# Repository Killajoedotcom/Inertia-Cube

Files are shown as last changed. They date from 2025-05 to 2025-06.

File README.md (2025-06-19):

## Welcome to the Inertia Cube Project!

INERTIA FOR GIT

The Inertia Cube (or i³) is a high speed FDM 3D printer that looks to optimize simplicity and provide a great entry point for all makers into the world of All Wheel Drive 3D printing. Its 300mm^3 build volume is built on a 3030 extrusion frame, optimized for ease of assembly, speed, and precision, while ensuring long-lasting performance and unmatched serviceability for enthusiasts who demand speed without compromising quality and those who need high printing uptime.

**World's first full kit printer featuring native Monolith Style Belt routing!** 

Thanks to the great work done over the last 2 years by CloakedWayne we have a fully optimized belt path for AWD printers that looks to minimize hardware and belt length, while providing incredible results in the process. We strongly encourage you to support his work via his [Kofi](https://ko-fi.com/cloakedwayne).

What makes it special? Some affectionately refer to the Inertia Cube as “baby’s first AWD printer” due to the simple assembly and design intent that makes it very easy to achieve near peak performance out of the printer regardless of DIY build experience.

Printer features:
- An external frame built from 3030 extrusions for extra rigidity
- Fixed gantry for maximum rigidity
- Easy Access electronics bay
- New extruder design which is a marriage of JaredC's G2SA and LDO's Orbiter2 parts to maximize extrusion force
- New single part toolhead design heavily inspired by Chirpy's Yavoth toolhead, optimized for rigidity and expanded compatibility
- Monolith AWD style gantry heavily inspired by CloakedWayne
- Linear rods for Y axis motion for easy install and simplicity
- 4 Z leadscrew motors for Quad Bed Leveling
- Support for USB or CAN Bus eddy current scanners as the Z probe (Beacon or Cartographer)
- Support for USB or CAN Bus Toolhead PCBs (LDO NH36, Fysetc H36, or BTT EBB36)
- Support for various hotends (starting with Rapido UHF, Dragon Ace Volcanao UHF, and Goliath)
- A latching sealed extrusion style front door

### FAQs:

**How do I stay up to date with this project?**

>Please Join our Discord here:
>
>Alt text for broken image link (https://discord.gg/da3cYmMA28)

**What is AWD (All Wheel Drive)?**
>While most CoreXY printers rely on a two-motor gantry drive system, the Inertia Cube leverages an advanced four-motor setup—two at the front and two at the back. This innovative design shortens the belt path, minimizes belt stretch, improves acceleration, and yields better input shaping results. With the added torque from the extra motors, acceleration performance is typically 1.5 times greater than traditional two-motor systems.

**What is the best performance hardware?**
>For optimal results, we recommend using LDO-42STH48-2504AH 1.8-degree motors paired with 20-tooth pulleys and EPDM GT2 belts if possible.

### Attributions
**Monolith Gantry** - [CloakedWayne](https://github.com/CloakedWayne/Monolith_Gantry_V2-VT)<br>
**Yavoth Toolhead** - [Chirpy](https://github.com/chirpy2605/voron/tree/main/V0/Yavoth)<br>
**G2** - [JaredC01](https://github.com/JaredC01/Galileo2)<br>
**Orbiter Project** - [Robert Lorincz](https://www.orbiterprojects.com/)<br>
**Clicky Clack** - [Whopping Pochard](https://github.com/tanaes/whopping_Voron_mods/tree/main/clickyclacky_door)<br>
**Inverted Electronics** - [LoganFraser](https://github.com/VoronDesign/VoronUsers/tree/main/printer_mods/LoganFraser/TridentInvertedElectronics)<br>

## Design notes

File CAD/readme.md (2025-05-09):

NOTE:<br>
<br>
Beta Frame Build is for those few people that have the 420mm horizontal and 555mm vertical 3030 extrusions. Some printed parts are resized to fit this build. Some fasteners and other non-printed parts still need to be added to this CAD model.<br>
<br>
Production Frame Build has been extended in XYZ to allow for a full 300mm cubic build volume, and will have 430mm horizontal and 600mm vertical 3030 extrusions. Contains all fasteners and other non-printed parts (although we are only human, and may have missed something).<br>

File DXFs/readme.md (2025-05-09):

NOTE:<br>
<br>
DXFs in the Beta folder are for those few people who have 420mm horizontal and 555mm vertical 3030 extrusions. They will NOT fit on a Production sized Inertia Cube build!<br>

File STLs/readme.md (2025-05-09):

STL Naming Convention:<br>
<br>
File name prefix:<br>
- "(a) ": part is designed to be printed in your accent color<br>
- "(d) ": part is designed to be printed with dual colors<br>
<br>
File name suffix:<br>
- " xN": print this part N times<br>

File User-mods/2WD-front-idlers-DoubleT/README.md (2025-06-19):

## Front Idlers - 2WD

This mod gives the opportunity to complete the build having only two steppers running X and Y while maintaining the original design to facilitate the convertion to 4WD when necessary. All needs to be done is replace the bottom plate with the stepper and voila!

### Images

<p align="center">
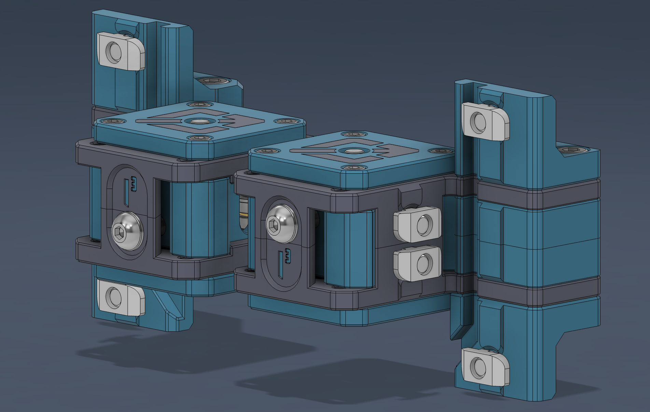
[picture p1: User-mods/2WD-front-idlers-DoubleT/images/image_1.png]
  
</p>

<p align="center">
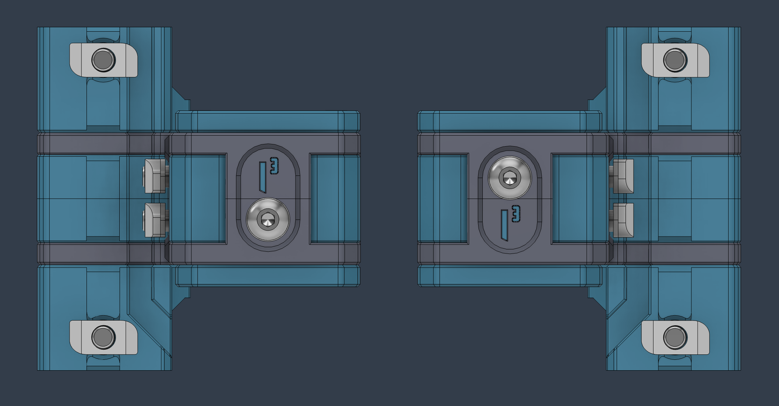
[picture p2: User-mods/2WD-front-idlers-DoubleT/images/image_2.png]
  
</p>

<p align="center">
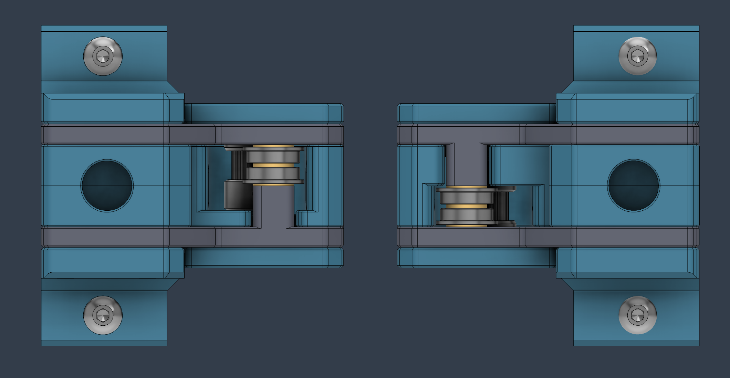
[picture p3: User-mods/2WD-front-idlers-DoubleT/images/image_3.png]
  
</p>

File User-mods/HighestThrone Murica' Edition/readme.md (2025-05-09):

>[!WARNING]
>these are American Themed Skirts for the Inertia Cube
>
>These skirts are considered "advanced" for most due to either using an ERCF or Manual Filament swaps
>

>[!IMPORTANT]
>Orca Slicer is the recommended slicer 





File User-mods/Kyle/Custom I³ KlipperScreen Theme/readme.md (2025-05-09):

Custom Inertia Cube Theme.

download and unzip theme,

put folder here:

klipperscreen theme install

>[!IMPORTANT]
>Make sure you restart klipper screen
>
>then find the theme on your touchscreen in klipperscreen options

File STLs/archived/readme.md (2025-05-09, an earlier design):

> [!IMPORTANT]
> All .stls current as of 8/26/2024
>
> If there are any issues please report them in the Inertia Cube Discord.
>
> Hotend parts do not have built-in supports, after rigorous testing we find that users slicer settings are best suited for these parts
>
> print all parts in the same orientation to ensure quality of fitment

> [!CAUTION]
> .stls
>  
>  it is YOUR responsibility to ensure the accuracy of YOUR printer.

>[!NOTE]
> Cable Chain folder, there are 3 versions, 2 bolt or 3 bolt pattern for your cable chain, and for 10x15 wider cable chains it is ONLY for 3 bolt

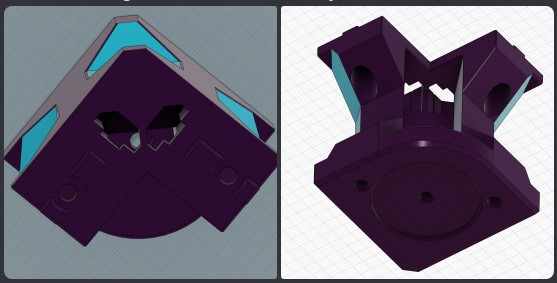
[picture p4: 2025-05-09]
User-mods/Steph/Wire Routing Feet/images/Wire Routing Feet.jpg

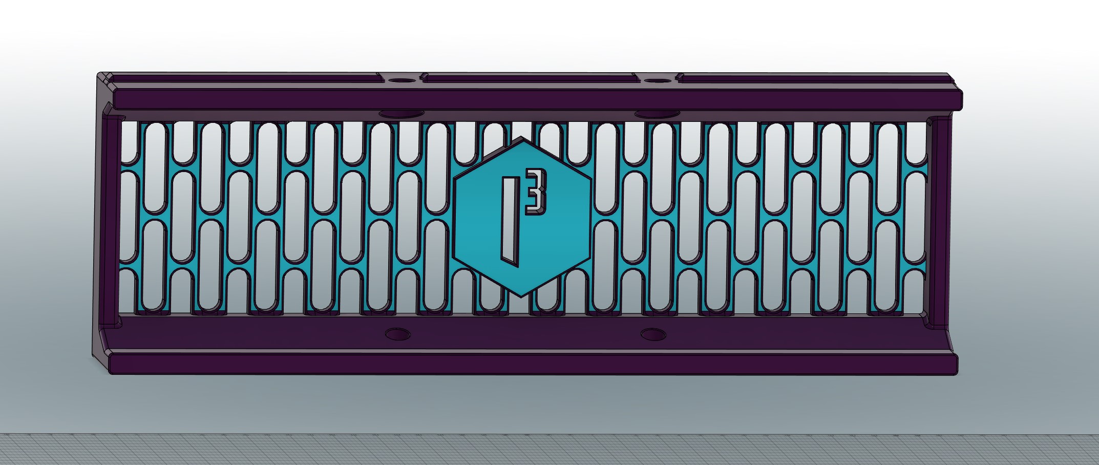
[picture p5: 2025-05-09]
User-mods/Steph/Modular Short Skirts/images/Wider Rear Center Skirt.jpg

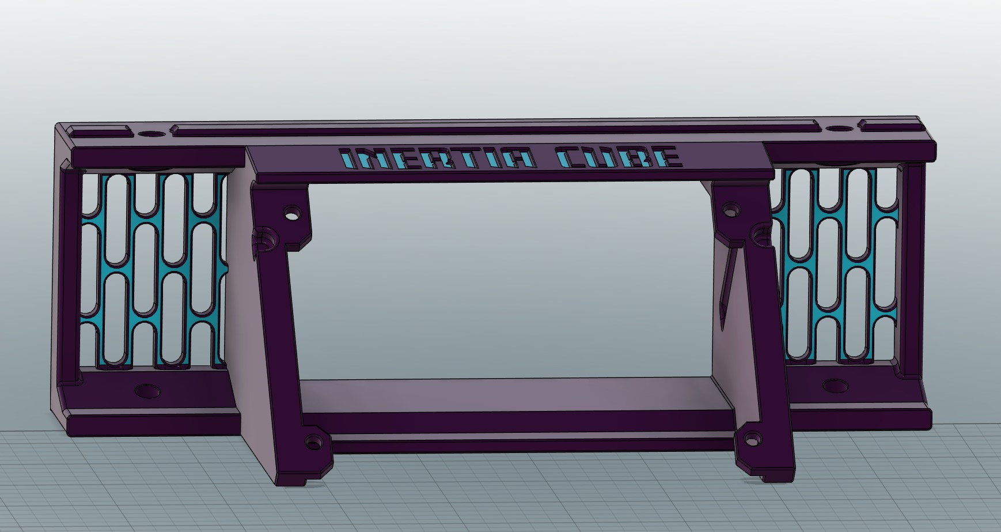
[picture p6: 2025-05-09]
User-mods/Steph/Modular Short Skirts/images/BTT PiTFT50 Extended Mount.jpg

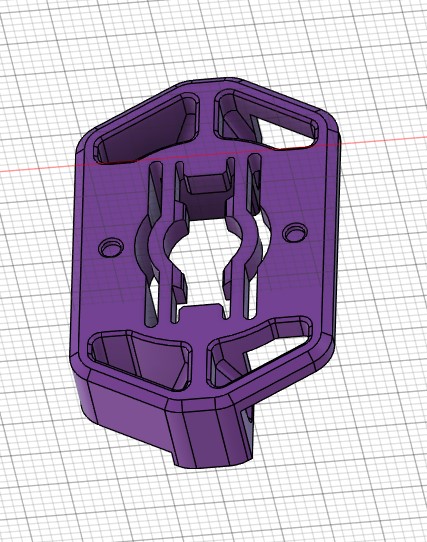
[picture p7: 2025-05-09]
User-mods/Steph/Annex Panel Clips for 3030 Extrusions/images/3030_lock_body_5.5mm.jpg

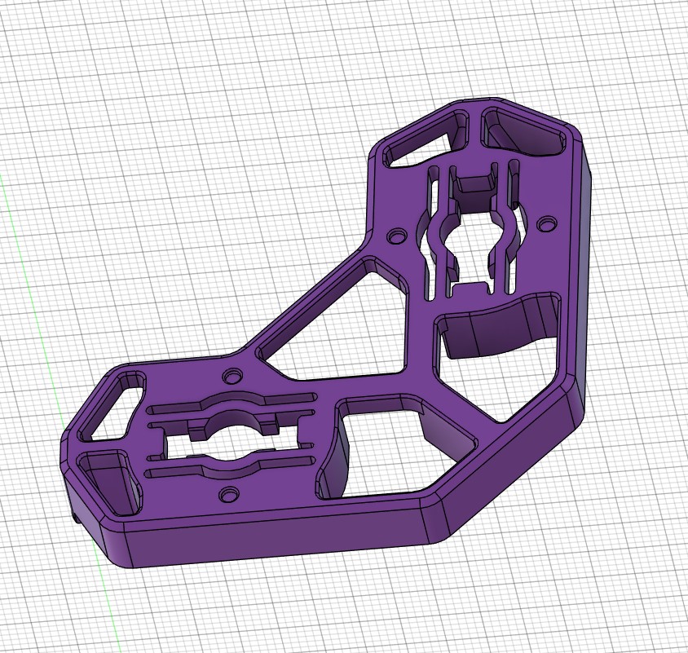
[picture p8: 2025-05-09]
User-mods/Steph/Annex Panel Clips for 3030 Extrusions/images/3030_corner_lock_body_5.5.jpg

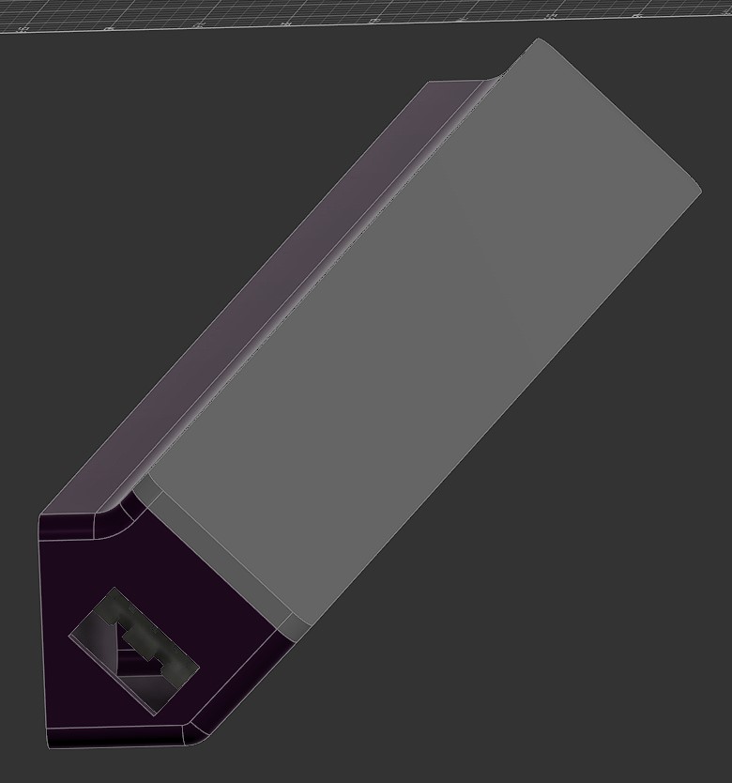
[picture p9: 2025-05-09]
User-mods/Steph/Daylight on a Stick Diffuser Mount/images/Daylight on a Stick Diffuser Mount.jpg

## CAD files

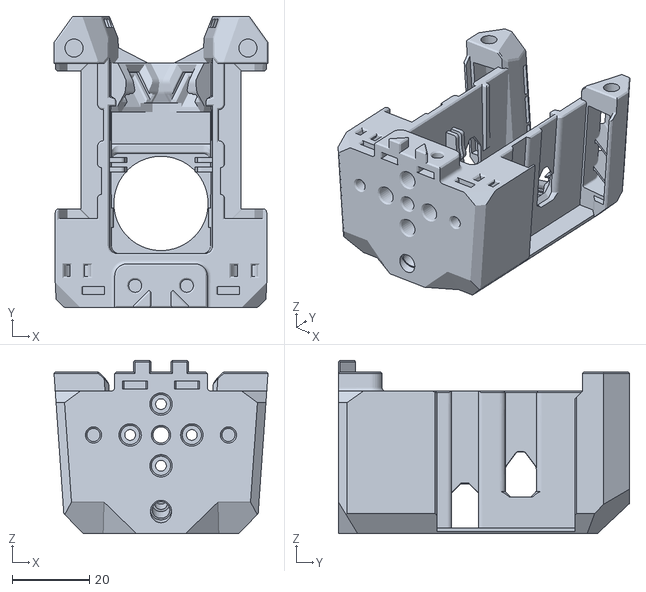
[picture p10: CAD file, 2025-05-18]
STLs/Production Frame Build/4. Monolithic Gantry/(d) Mainbody - Rapido UHF.stl
55.5 x 75.5 x 45.0

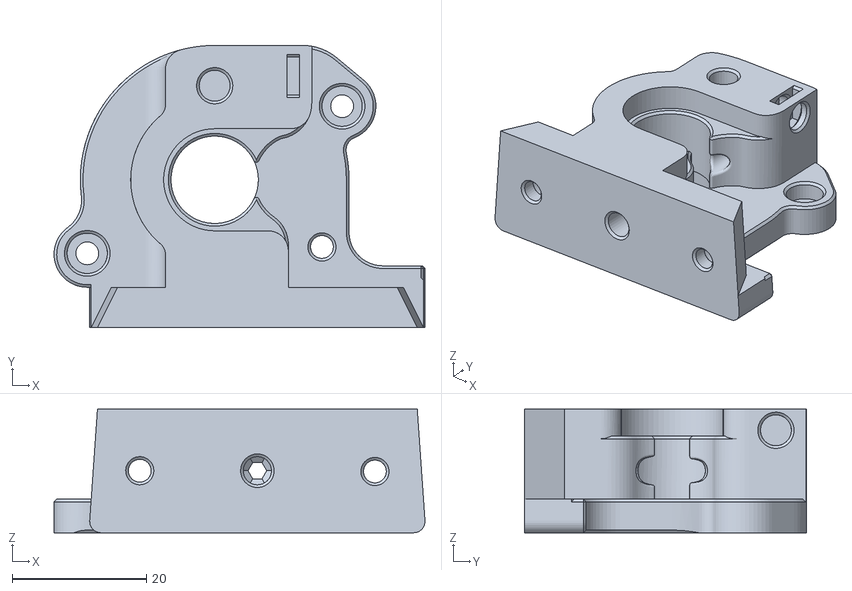
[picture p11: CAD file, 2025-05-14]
STLs/Production Frame Build/4. Monolithic Gantry/Extruder Main Body.stl
55.2 x 42.0 x 18.4

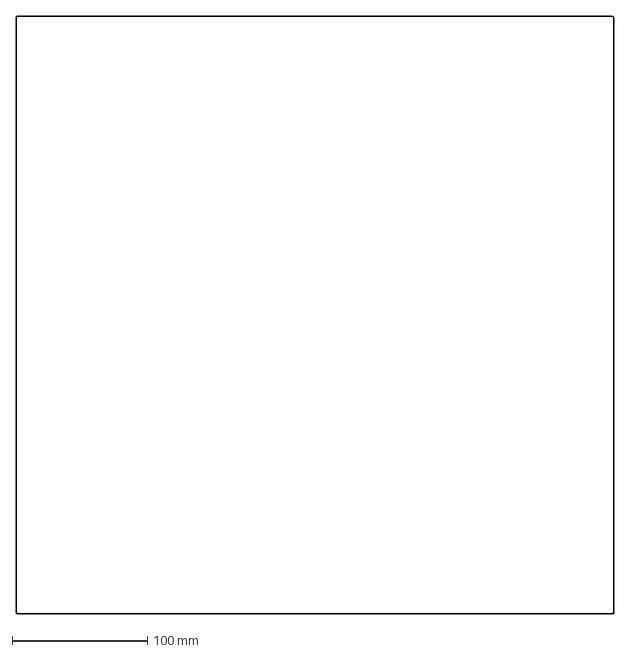
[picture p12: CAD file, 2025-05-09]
DXFs/Beta/Inertia Cube Beta Top Panel.dxf
442.0 x 442.0 mm

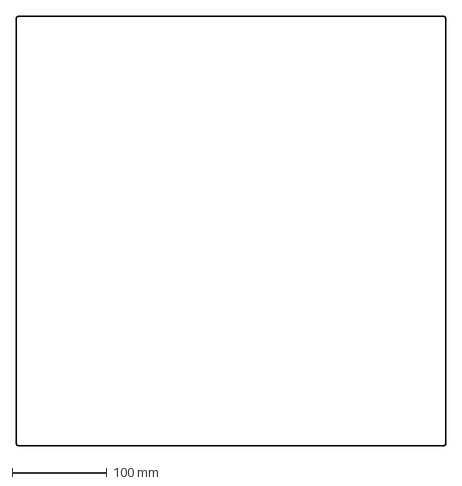
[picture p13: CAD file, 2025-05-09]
DXFs/Inertia Cube Top Panel.dxf
452.0 x 452.0 mm

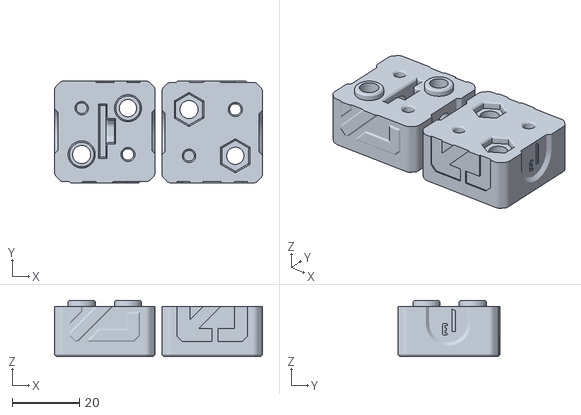
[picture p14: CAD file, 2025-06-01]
STLs/Inertia Calibration Cube/Inertia Calibration Cube.stl
62.0 x 30.4 x 16.8

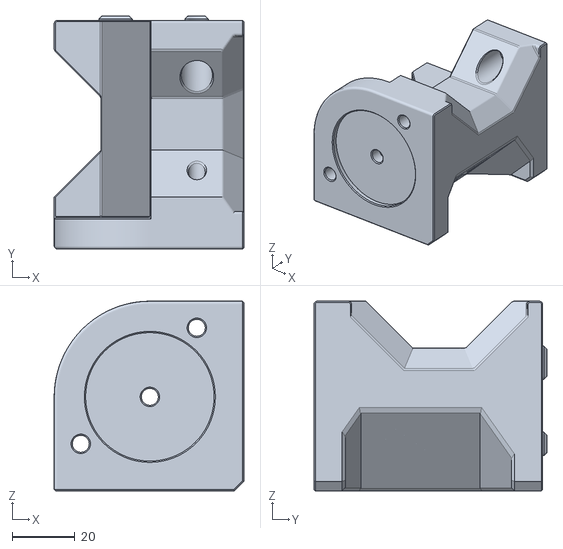
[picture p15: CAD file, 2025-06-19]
STLs/Production Frame Build/2. Skirts/(a) Foot x4.stl
60.5 x 74.4 x 60.6

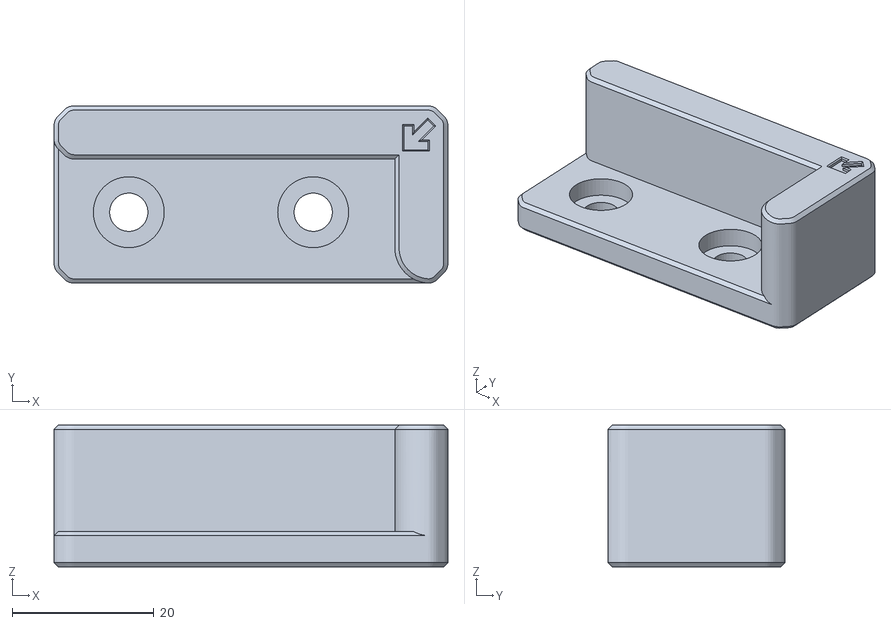
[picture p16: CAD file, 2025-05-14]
STLs/Production Frame Build/3. Z Axis/(a) Rear Right Build Sheet Alignment Guide.stl
55.5 x 25.0 x 20.0

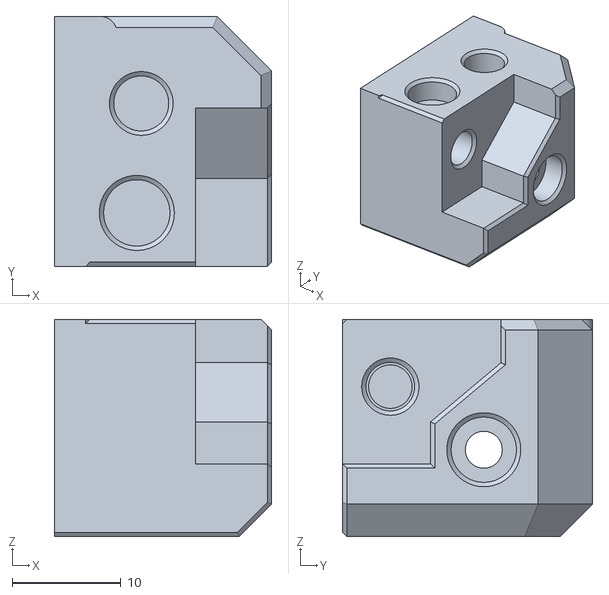
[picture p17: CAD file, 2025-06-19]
STLs/Production Frame Build/5. Lock Latch Door/Lock Latch 2020 Upper Mount.stl
20.0 x 23.0 x 20.0

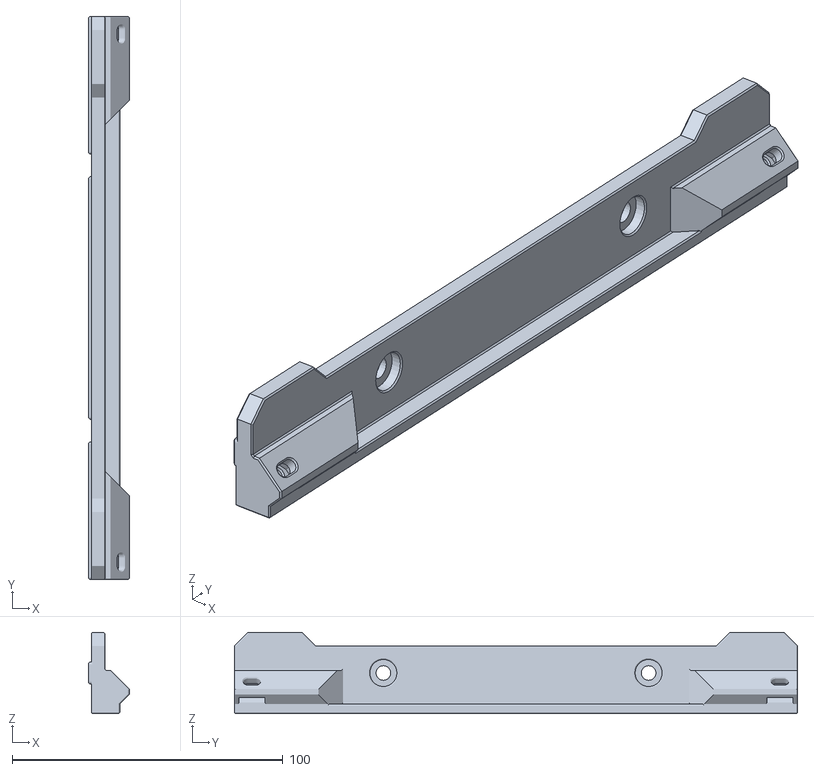
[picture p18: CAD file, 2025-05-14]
STLs/Production Frame Build/6. Electronics/Upper Frame Daylight - Disco LED Mount x2.stl
15.0 x 208.0 x 30.0

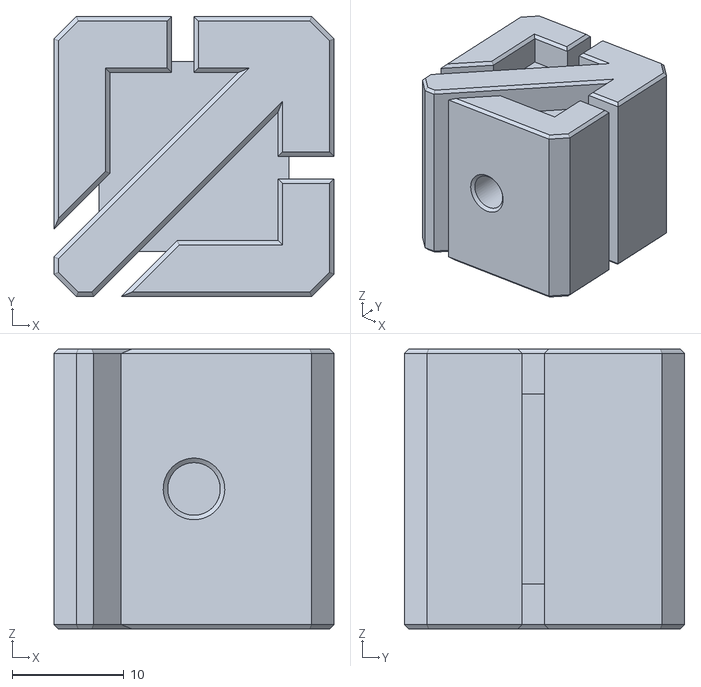
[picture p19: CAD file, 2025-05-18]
STLs/Production Frame Build/7. Panels/(d) Deck Panel Handle.stl
25.0 x 25.0 x 25.0

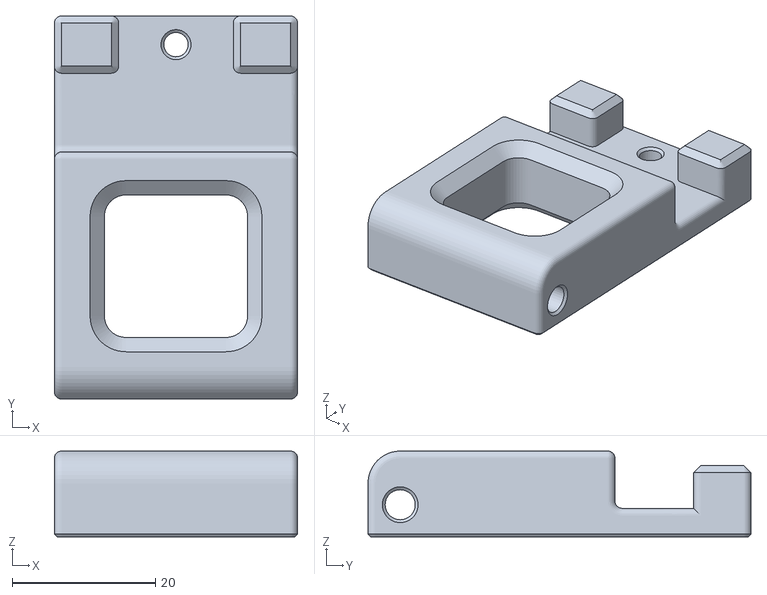
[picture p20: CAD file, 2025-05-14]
STLs/Production Frame Build/8. Filament Guide/(a) Filament Guide.stl
34.0 x 53.5 x 12.0

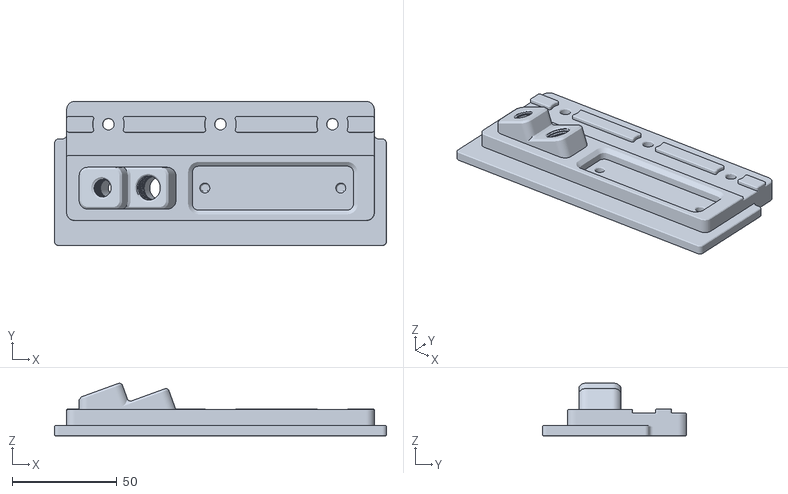
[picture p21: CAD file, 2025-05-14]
STLs/Production Frame Build/9. Rear Exhaust Plate/Exhaust Plate.stl
158.6 x 69.0 x 25.3

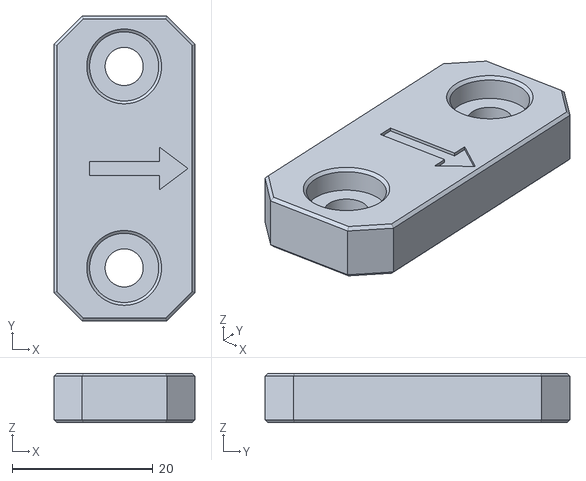
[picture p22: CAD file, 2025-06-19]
STLs/Production Frame Build/Tools/Dual_Belt_Holder_Cover_RevB.STL
20.0 x 43.2 x 7.00

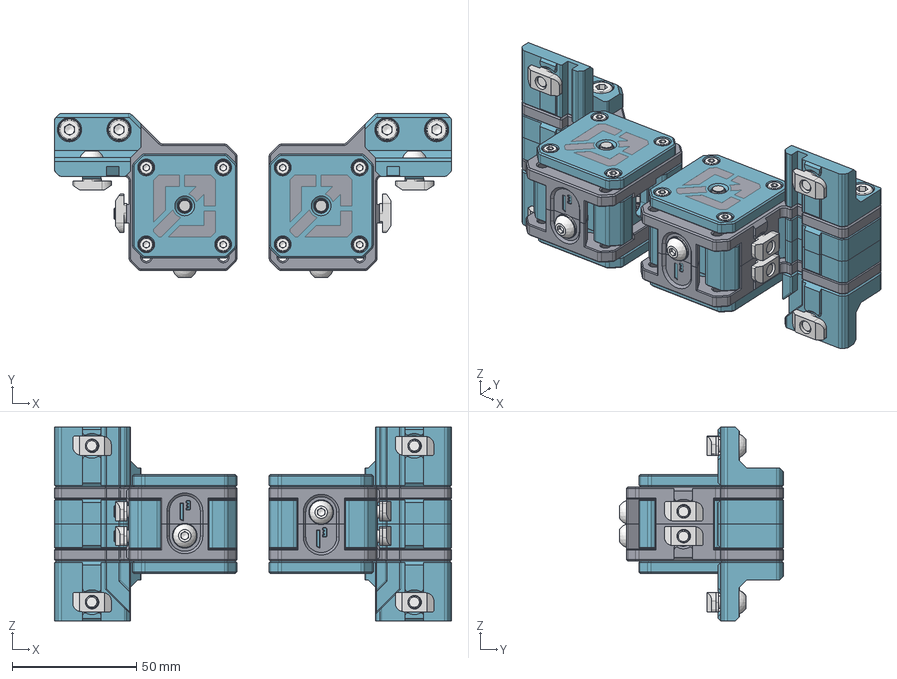
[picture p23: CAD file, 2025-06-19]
User-mods/2WD-front-idlers-DoubleT/CAD/Innertia Cube - 2WD - Front Idlers.step
160.0 x 66.1 x 78.0 mm
front left motor hardware (12)
front left motor hardware (17)
Front Left Motor
D5x30 smooth pin x 2
front left motor hardware (7)
front left motor hardware (1) x 2
Spacer A x 2
Spacer B x 2
front left motor hardware (16)
front left motor hardware (6)
front left motor hardware (11)
Socket button head screw M5x0.8 x 8_1
Socket button head screw M5x0.8 x 8
front left motor hardware (9)
front left motor hardware (14)
front left motor hardware (18)
front left motor hardware (4)
front left motor hardware (20)
front left motor hardware
front left motor hardware (8)
front left motor hardware (3)
M5 3030 Drop-in T-Nut (1) (2) (1) (1) (1)
M5 3030 Drop-in T-Nut (1) (2) (2) (1)
M5 3030 Drop-in T-Nut (1) (1) (1) (1)
M5 3030 Drop-in T-Nut (1) (3) (1)
m5 flat nut v1
M3xD5x4 threaded insert x 8
front left motor hardware (10)
front left motor hardware (13)
front left motor hardware (2)
front left motor hardware (15)
front right motor hardware (23) x 2
front right motor hardware (23)_1 x 4
Front Left Top Brace2
front rail mount b_1
front rail mount a_1
Front Left Bottom Brace (1)
Document
Document_2
Double Shear Retainer77_2_3
Double Shear Retainer77_2_3_1
Left Tensioner Block73
front right motor hardware (15)
front right motor hardware (9)
front right motor hardware (10)
front right motor hardware (22)
front right motor hardware (5)
front right motor hardware (17)
front right motor hardware (12)
front right motor hardware (2)
front right motor hardware (21)
front right motor hardware (1)
front right motor hardware (14)
front right motor hardware (7)
M5 3030 Drop-in T-Nut (1) (2) (1) (1) (1) (1)
M5 3030 Drop-in T-Nut (1) (3) (1) (1)
M5 3030 Drop-in T-Nut (1) (1) (1) (1) (1)
M5 3030 Drop-in T-Nut (1) (2) (2) (1) (1)
front right motor hardware (19)
front right motor hardware (16)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

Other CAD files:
User-mods/2020_front_latch_upper.stl
User-mods/2WD-front-idlers-DoubleT/STLs/Pulley Tool.stl
User-mods/HighestThrone Murica' Edition/Murica' skirts/front stars.STL
User-mods/Seb/Skirt/CAD/Skirt Corner Foot.step
DXFs/Beta/Inertia Cube Beta Bottom Panel.dxf
DXFs/Beta/Inertia Cube Beta Deck Panel.dxf
DXFs/Beta/Inertia Cube Beta Door Panel.dxf
DXFs/Beta/Inertia Cube Beta Rear Panel.dxf
DXFs/Beta/Inertia Cube Beta Side Panel x2.dxf
DXFs/Inertia Cube Bottom Panel.dxf
DXFs/Inertia Cube Deck Panel.dxf
DXFs/Inertia Cube Door Panel.dxf
DXFs/Inertia Cube Rear Panel.dxf
DXFs/Inertia Cube Side Panel x2.dxf
STLs/Production Frame Build/2. Skirts/(a) BTT PiTFT50 Screen Cover.stl
STLs/Production Frame Build/2. Skirts/(a) Skirt End Cover x8.stl
STLs/Production Frame Build/2. Skirts/(a) Skirt Middle Cover x4.stl
STLs/Production Frame Build/2. Skirts/(d) Fan Cover x4.stl
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

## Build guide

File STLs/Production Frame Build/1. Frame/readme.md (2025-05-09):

No printed parts are needed for the Frame build, but I didn't want to start the directory list with 2. ;-)

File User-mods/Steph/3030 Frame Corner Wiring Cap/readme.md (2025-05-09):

# 3030 Frame Corner Wiring Cap

I designed these because I wanted to run LED wires in the inside extrusions slots around the top of the frame, and the wires then needed to "jump" over the corner Z extrusion to the next extrusion slot.

This part makes it so that you can do that, and no wires are visible.

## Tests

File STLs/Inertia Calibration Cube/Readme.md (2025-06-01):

# Inertia Calibration Cube

This is a calibration cube that encapsulates the entire printer design aspects that involve tuning and challenges to the printed parts.

### The Cube includes the following printed features:

- M5 and M3 Bolt througholes with captured M5 and M3 nuts respectively
- 5x30mm and 3x20mm press fit pin slots
- M5 Flat T-nut slot to mimmick tensioner block
- Cut and Extruded Inertia Cube Logos
- Alignment nubs for seamless alignemnt
- Print in Place in support

Print in the same orientation as imported into slicer.

**If you can print this cube and the tolerances match the intended purpose above, you should have zero issues printing the parts for the printer.**

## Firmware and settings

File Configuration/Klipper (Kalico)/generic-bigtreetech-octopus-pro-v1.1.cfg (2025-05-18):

# This file contains common pin mappings for the BigTreeTech Octopus
# and Octopus Pro boards. To use this config, start by identifying the
# micro-controller on the board - it may be an STM32F446, STM32F429,
# or an STM32H723.  Select the appropriate micro-controller in "make
# menuconfig" and select "Enable low-level configuration options". For
# STM32F446 boards the firmware should be compiled with a "32KiB
# bootloader" and a "12MHz crystal" clock reference. For STM32F429
# boards use a "32KiB bootloader" and an "8MHz crystal". For STM32H723
# boards use a "128KiB bootloader" and a "25Mhz crystal".

# See docs/Config_Reference.md for a description of parameters.

# Driver0
[stepper_x]
step_pin: PF13
dir_pin: PF12
enable_pin: !PF14
microsteps: 16
rotation_distance: 40
endstop_pin: PG6
position_endstop: 0
position_max: 200
homing_speed: 50

# Driver1
[stepper_y]
step_pin: PG0
dir_pin: PG1
enable_pin: !PF15
microsteps: 16
rotation_distance: 40
endstop_pin: PG9
position_endstop: 0
position_max: 200
homing_speed: 50

# Driver2
[stepper_z]
step_pin: PF11
dir_pin: PG3
enable_pin: !PG5
microsteps: 16
rotation_distance: 8
endstop_pin: PG10
position_endstop: 0.5
position_max: 200

# Driver3
# The Octopus only has 4 heater outputs which leaves an extra stepper
# This can be used for a second Z stepper, dual_carriage, extruder co-stepper,
# or other accesory such as an MMU
#[stepper_]
#step_pin: PG4
#dir_pin: PC1
#enable_pin: PA2
#endstop_pin: PG11
#...

# Driver4
[extruder]
step_pin: PF9
dir_pin: PF10
enable_pin: !PG2
microsteps: 16
rotation_distance: 33.500
nozzle_diameter: 0.400
filament_diameter: 1.750
heater_pin: PA0 # HE0
sensor_pin:  PF4 # T0
sensor_type: EPCOS 100K B57560G104F
control: pid
pid_Kp: 22.2
pid_Ki: 1.08
pid_Kd: 114
min_temp: 0
max_temp: 250

#[filament_switch_sensor material_0]
#switch_pin: PG12

# Driver5
#[extruder1]
#step_pin: PC13
#dir_pin: PF0
#enable_pin: !PF1
#heater_pin: PA3 # HE1
#sensor_pin: PF5 # T1
#...

#[filament_switch_sensor material_1]
#switch_pin: PG13

# Driver6
#[extruder2]
#step_pin: PE2
#dir_pin: PE3
#enable_pin: !PD4
#heater_pin: PB0 # HE2
#sensor_pin: PF6 # T2
#...

#[filament_switch_sensor material_2]
#switch_pin: PG14

# Driver7
#[extruder3]
#step_pin: PE6
#dir_pin: PA14
#enable_pin: !PE0
#heater_pin: PB11 # HE3
#sensor_pin: PF7 # T3
#...

#[filament_switch_sensor material_3]
#switch_pin: PG15

[heater_bed]
heater_pin: PA1
sensor_pin: PF3 # TB
sensor_type: ATC Semitec 104GT-2
control: watermark
min_temp: 0
max_temp: 130

[fan]
pin: PA8

#[heater_fan fan1]
#pin: PE5

#[heater_fan fan2]
#pin: PD12

#[heater_fan fan3]
#pin: PD13

#[heater_fan fan4]
#pin: PD14

#[controller_fan fan5]
#pin: PD15

[mcu]
serial: /dev/serial/by-id/usb-Klipper_Klipper_firmware_12345-if00
# CAN bus is also available on this board

[printer]
kinematics: cartesian
max_velocity: 300
max_accel: 3000
max_z_velocity: 5
max_z_accel: 100

########################################
# TMC2209 configuration
########################################

#[tmc2209 stepper_x]
#uart_pin: PC4
##diag_pin: PG6
#run_current: 0.800
#stealthchop_threshold: 999999

#[tmc2209 stepper_y]
#uart_pin: PD11
##diag_pin: PG9
#run_current: 0.800
#stealthchop_threshold: 999999

#[tmc2209 stepper_z]
#uart_pin: PC6
##diag_pin: PG10
#run_current: 0.650
#stealthchop_threshold: 999999

#[tmc2209 stepper_]
#uart_pin: PC7
##diag_pin: PG11
#run_current: 0.650
#stealthchop_threshold: 999999

#[tmc2209 extruder]
#uart_pin: PF2
#run_current: 0.800
#stealthchop_threshold: 999999

#[tmc2209 extruder1]
#uart_pin: PE4
#run_current: 0.800
#stealthchop_threshold: 999999

#[tmc2209 extruder2]
#uart_pin: PE1
#run_current: 0.800
#stealthchop_threshold: 999999

#[tmc2209 extruder3]
#uart_pin: PD3
#run_current: 0.800
#stealthchop_threshold: 999999

########################################
# TMC2130 configuration
########################################

#[tmc2130 stepper_x]
#cs_pin: PC4
#spi_bus: spi1
##diag1_pin: PG6
#run_current: 0.800
#stealthchop_threshold: 999999

#[tmc2130 stepper_y]
#cs_pin: PD11
#spi_bus: spi1
##diag1_pin: PG9
#run_current: 0.800
#stealthchop_threshold: 999999

#[tmc2130 stepper_z]
#cs_pin: PC6
#spi_bus: spi1
##diag1_pin: PG10
#run_current: 0.650
#stealthchop_threshold: 999999

#[tmc2130 stepper_]
#cs_pin: PC7
#spi_bus: spi1
##diag1_pin: PG11
#run_current: 0.800
#stealthchop_threshold: 999999

#[tmc2130 extruder]
#cs_pin: PF2
#spi_bus: spi1
#run_current: 0.800
#stealthchop_threshold: 999999

#[tmc2130 extruder1]
#cs_pin: PE4
#spi_bus: spi1
#run_current: 0.800
#stealthchop_threshold: 999999

#[tmc2130 extruder2]
#cs_pin: PE1
#spi_bus: spi1
#run_current: 0.800
#stealthchop_threshold: 999999

#[tmc2130 extruder3]
#cs_pin: PD3
#spi_bus: spi1
#run_current: 0.800
#stealthchop_threshold: 999999

[board_pins]
aliases:
    # EXP1 header
    EXP1_1=PE8, EXP1_2=PE7,
    EXP1_3=PE9, EXP1_4=PE10,
    EXP1_5=PE12, EXP1_6=PE13,    # Slot in the socket on this side
    EXP1_7=PE14, EXP1_8=PE15,
    EXP1_9=<GND>, EXP1_10=<5V>,

    # EXP2 header
    EXP2_1=PA6, EXP2_2=PA5,
    EXP2_3=PB1, EXP2_4=PA4,
    EXP2_5=PB2, EXP2_6=PA7,      # Slot in the socket on this side
    EXP2_7=PC15, EXP2_8=<RST>,
    EXP2_9=<GND>, EXP2_10=PC5

# See the sample-lcd.cfg file for definitions of common LCD displays.

# A [probe] section can be defined instead with a pin: setting identical
# to the sensor_pin: for a bltouch
#[bltouch]
#sensor_pin: PB7
#control_pin: PB6
#z_offset: 0

#[neopixel my_neopixel]
#pin: PB10

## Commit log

2025-05-09 Transfer from old repo
    [(a) Annex Clips 3030 Key Asymmetric 5.5mm x46.stl, (a) BTT EBB36 Mount.stl, (a) Clicky Clack 3030 Latch Plate.stl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]
2025-05-11 Updating CAD
2025-05-14 Reorient All STLS
    [(a) Annex Clips 3030 Key Asymmetric 5.5mm x46.stl, (a) BTT EBB36 Mount.stl, (a) Clicky Clack 3030 Latch Plate.stl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]
2025-05-14 More CAD updates
2025-05-14 CAD updates
2025-05-18 Move Mods and housecleaning
    [3030 Frame Corner Wiring Cap v3.step, 3030 Frame Corner Wiring Cap v3_Inertia Cube Mods v10_One Piece_1_Body1.stl, 3030 Frame Corner Wiring Cap v3_Inertia Cube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]
2025-05-18 Updating CAD and STLs
    New Skirt parts and Deck Panel handle
    [(a) BTT PiTFT50 Screen Cover.stl, (a) Fan Cover x4.stl, (a) Foot x4.stl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]
2025-05-18 archiving old beta User-Mods
    [3030 Frame Corner Wiring Cap v3.step, 3030 Frame Corner Wiring Cap v3_Inertia Cube Mods v10_One Piece_1_Body1.stl, 3030 Frame Corner Wiring Cap v3_Inertia Cube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]
2025-05-18 Updating CAD with easy to print toolhead logo
    [(d) Mainbody - Rapido UHF.stl, Mainbody - Rapido UHF.stl]
2025-05-18 Reoriented STLs
    [(a) Foot x4.stl, (a) Skirt End Cover x8.stl, (a) Skirt Middle Cover x4.stl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]
2025-05-18 Adding some config files
    Not done editing/combining these yet, but it's a start
    [generic-bigtreetech-octopus-pro-v1.1.cfg, nitehawk-36.cfg, sample-macros.cfg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]
2025-05-18 Adding tool STLs
    [2020_mgn12_guide_(x3).stl, 3030_mgn12_guide_(x3).stl, MGN12 Greaser - Rail v4.stl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]
2025-06-12 Replaced Clicky Clack with Lock Latch Door Parts
    [(a) Clicky Clack 3030 Latch Plate.stl, (a) Clicky Clack Bottom Latch.stl, (a) Clicky Clack Middle Latch.stl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]
2025-06-15 Uploaded Belt Pulling Tool
    Belt Pulling Tool added to "tools" section
    [Dual_Belt_Holder_Base_RevB.STL, Dual_Belt_Holder_Cover_RevB.STL]
